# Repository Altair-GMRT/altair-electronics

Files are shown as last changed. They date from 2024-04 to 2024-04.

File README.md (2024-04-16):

# **altair-electronics**

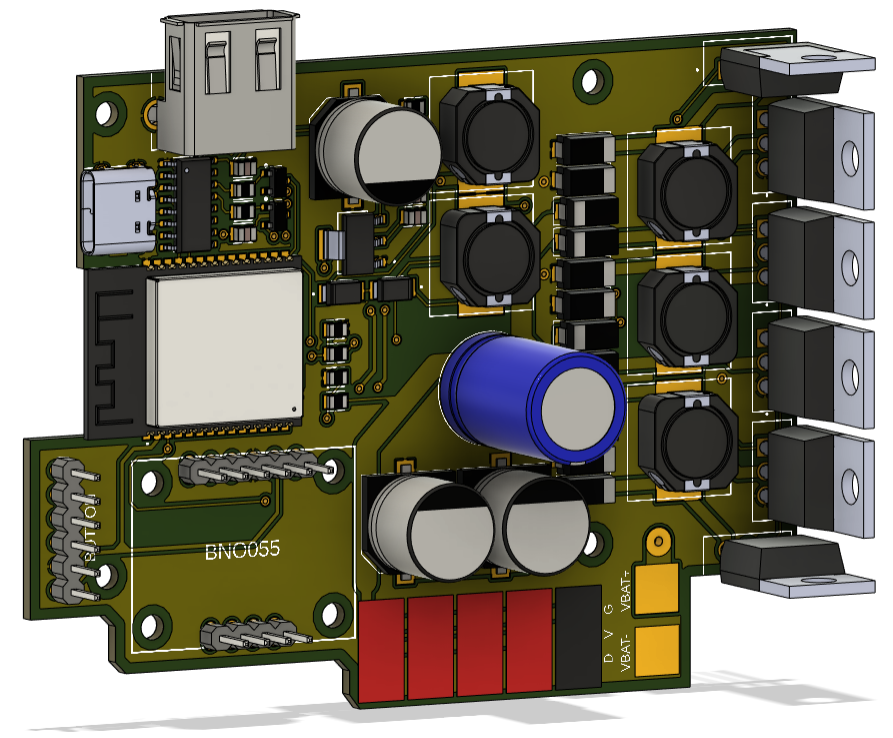
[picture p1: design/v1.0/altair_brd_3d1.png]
Board View 1

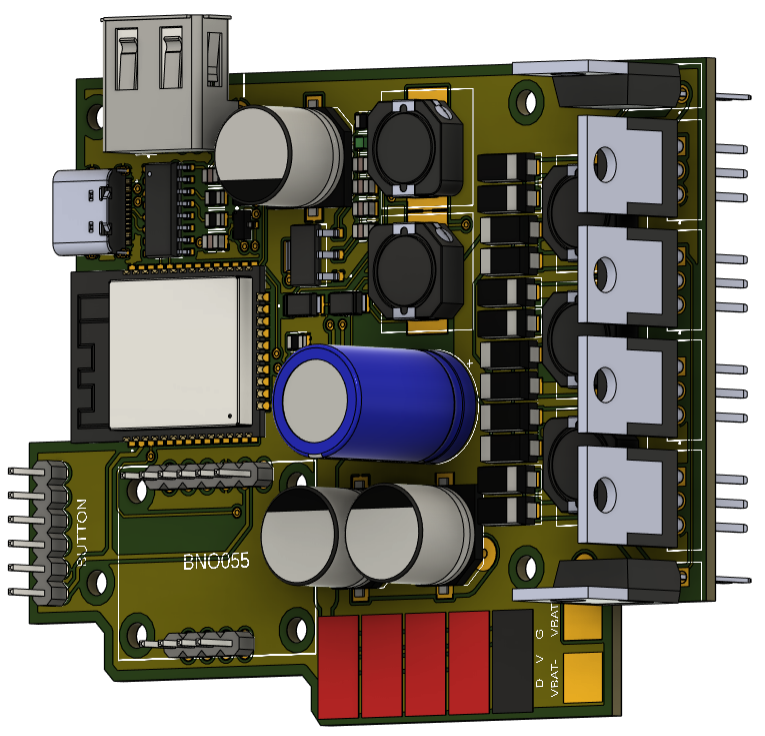
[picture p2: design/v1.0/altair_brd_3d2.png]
Board View 2

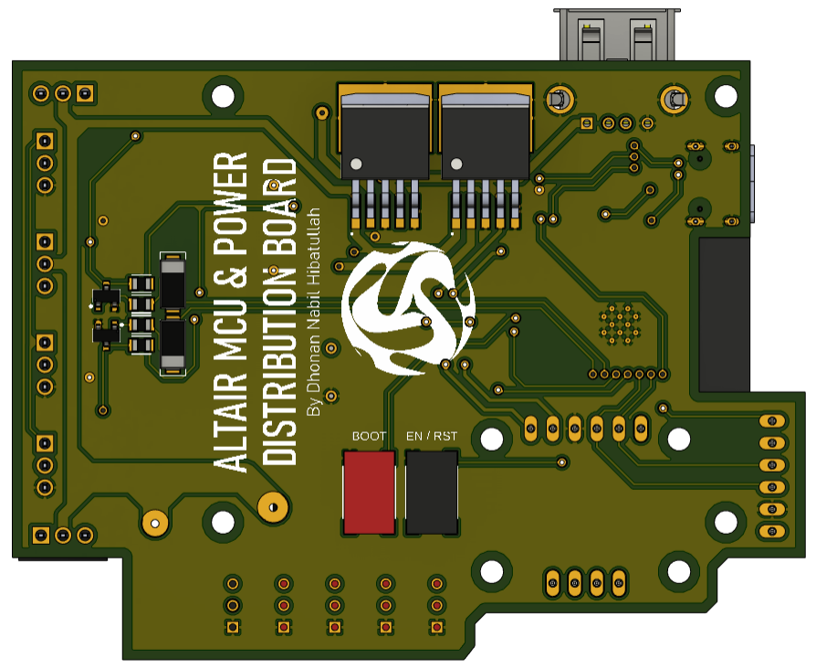
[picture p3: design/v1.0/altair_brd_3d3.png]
Board View 3


## **1. Contents**

- **altair-mcu/**

    This folder contains the Arduino IDE source code for the Altair MCU's firmware. Make sure the following libraries have been installed on your IDE before compiling:

    1. [**Adafruit GFX**](https://github.com/adafruit/Adafruit-GFX-Library)
    2. [**Adafruit SSD1306**](https://github.com/adafruit/Adafruit_SSD1306)
    3. [**Adafruit Sensor**](https://github.com/adafruit/Adafruit_Sensor)
    4. [**Adafruit BNO055**](https://github.com/adafruit/Adafruit_BNO055)

- **design/**

    This folder contains the Eagle/Fusion schematics and board designs, including the libraries used.

## **2. Electronics Design**
The robot will be powered by 4s 35c 5200mAh Li-Po battery. Hence, the battery voltage will be in the range of 12.8V - 16.8V with a maximum discharge of 182A. The Raspberry Pi 5 needs 5V 5A power supply, and 20 Dynamixel MXs need 14V 2A per servo. We will convert the battery voltage to supply those two with a 5V regulator and a Buck-Boost Converter, respectively. Read more about the design at ```design/simulations```.

### **2.1 Buck-Boost Converter**
The buck and the boost in the Buck-Boost Converter will be used interchangeably. The equation describing the behaviour of the buck is:

$$V_{out} = DV_{in}$$

$$I_{ripple} = V_{out}\left(\frac{1}{R} \pm \frac{1 - D}{2L}T \right)$$

$$V_{ripple} \propto \frac{(1-D)V_{out}T^2}{8LC}$$

and for the boost:

$$V_{out} = \frac{1}{1 - D}V_{in}$$

$$I_{ripple} = V_{in}\left(\frac{1}{R(1-D)^2} \pm \frac{1}{2L}DT\right)$$

$$V_{ripple} \propto \frac{DTV_{out}}{RC}$$

Consider the following table: 

|No.|Parameter|Value|
|:---:|:---:|:---:|
|1|$D_{buck}$|$[0.83, 1]$|
|2|$D_{boost}$|$[0, 0.086]$|
|3|$V_{in}$|$[12.8, 16.8]\text{V}$|
|4|$V_{out}$|$14\text{V}$|
|5|$I_{max}$|$30\text{A}$|
|6|$T_S$|$12.5\mu\text{s}$|
|7|$f_S$|$80\text{kHz}$|
|8|$R$|$V_{out}/I_{max} = 0.5\Omega$|

We obtain the optimal (smallest possible, yet acceptable performance) value of $L = 330\mu\text{H}$ and $C = 4.7\text{mF}$ in 3 parallels.

### **2.2 Components**
The following table shows the entire components required for assembling a complete circuit.

| No. | Component Name | Qty. | Datasheets |
| :---: | :--- | :---: | :---: |
| 1 | **ESP32-WROOM-32D** | | |
| 2 | **BNO055** 9-Axis IMU | | |
| 3 | **SSD1306** OLED Display | | |
| 4 | **LM2596S-5.0** 5V 3A Regulator | | |
| 5 | **1N5824** Schottky Diode | | |
| 6 | **CDRH127R** Power Inductor | | |
| 7 | **IRF9540** P-Channel Power MOSFET | | |
| 8 | **S9013** NPN Transistor | | |
| 9 | **SR5100 & 1N58219** Schottky Diode | | |
| 10 | **MOLEX 22-03-5035** Dynamixel Connector | | |
| 11 | **USB Female Type-C** | | |
| 12 | **USB Female Type-A** | | |
| 13 | **SMD Button** | | |

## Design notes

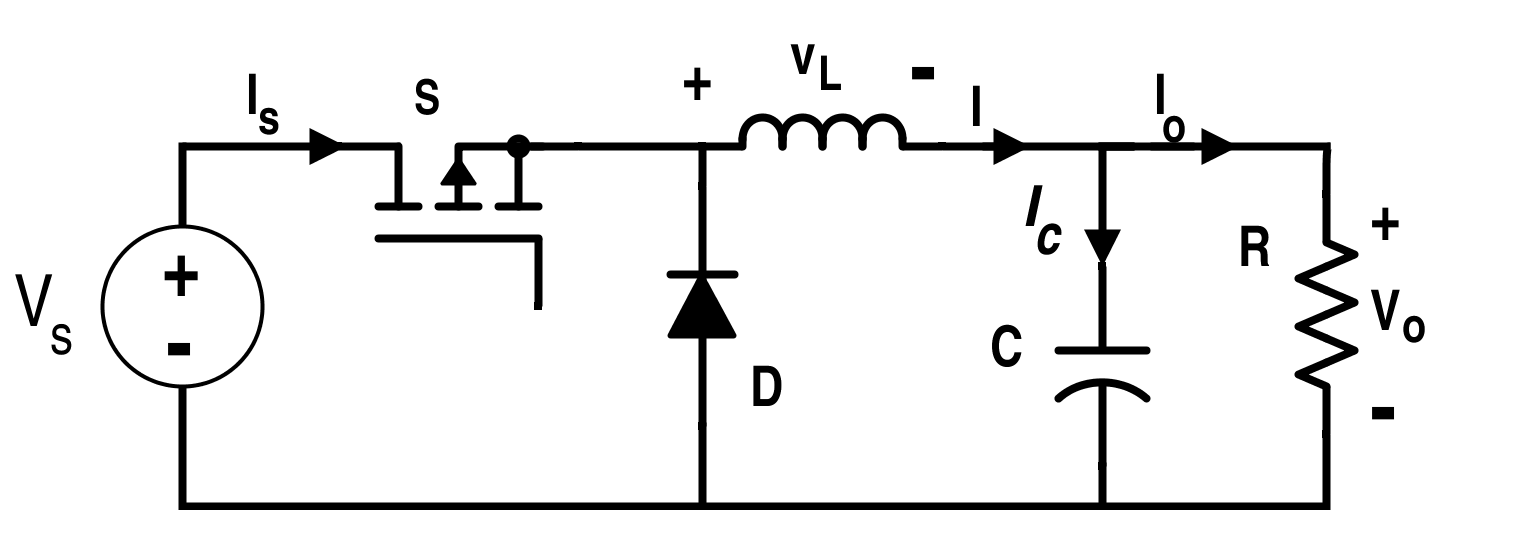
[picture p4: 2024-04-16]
design/simulations/assets/buck_converter.jpg

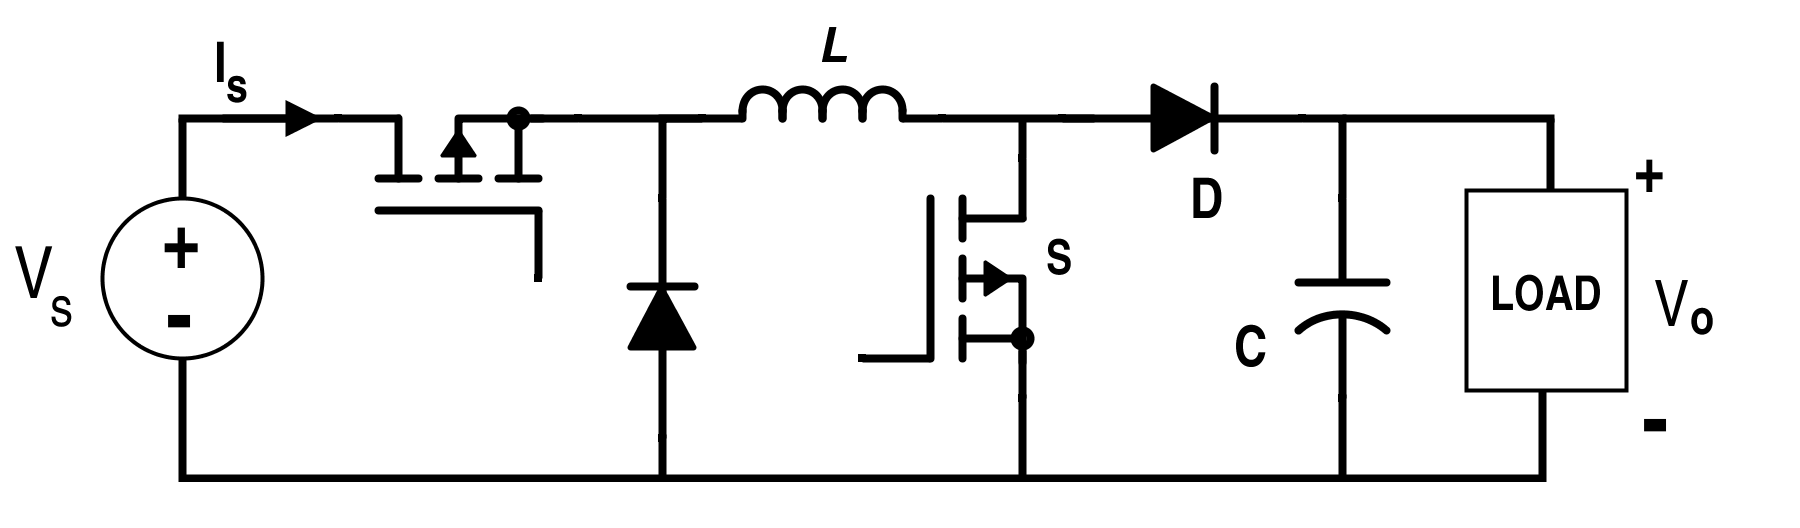
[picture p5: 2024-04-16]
design/simulations/assets/buck_boost_converter.jpg

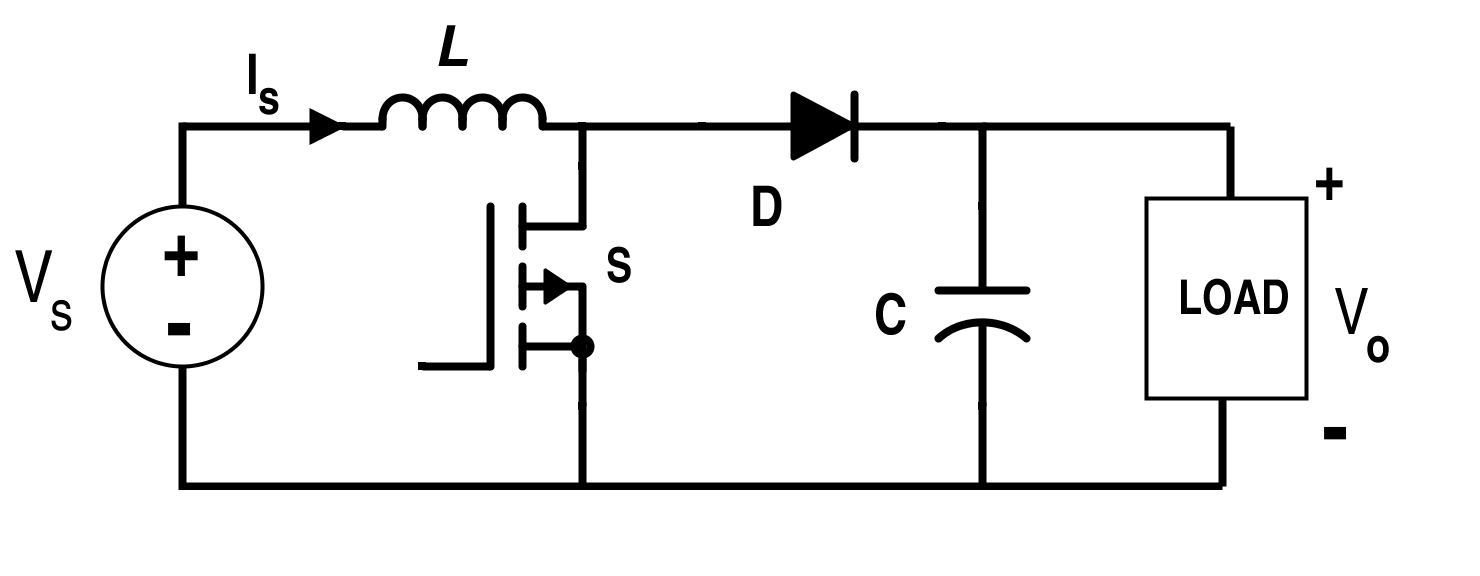
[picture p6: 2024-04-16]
design/simulations/assets/boost_converter.jpg

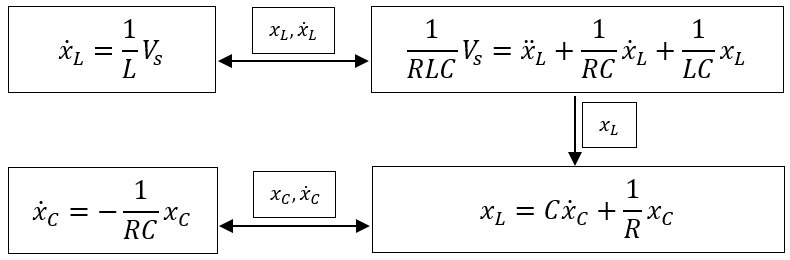
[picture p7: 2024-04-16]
design/simulations/assets/boost_sim_diagram.png

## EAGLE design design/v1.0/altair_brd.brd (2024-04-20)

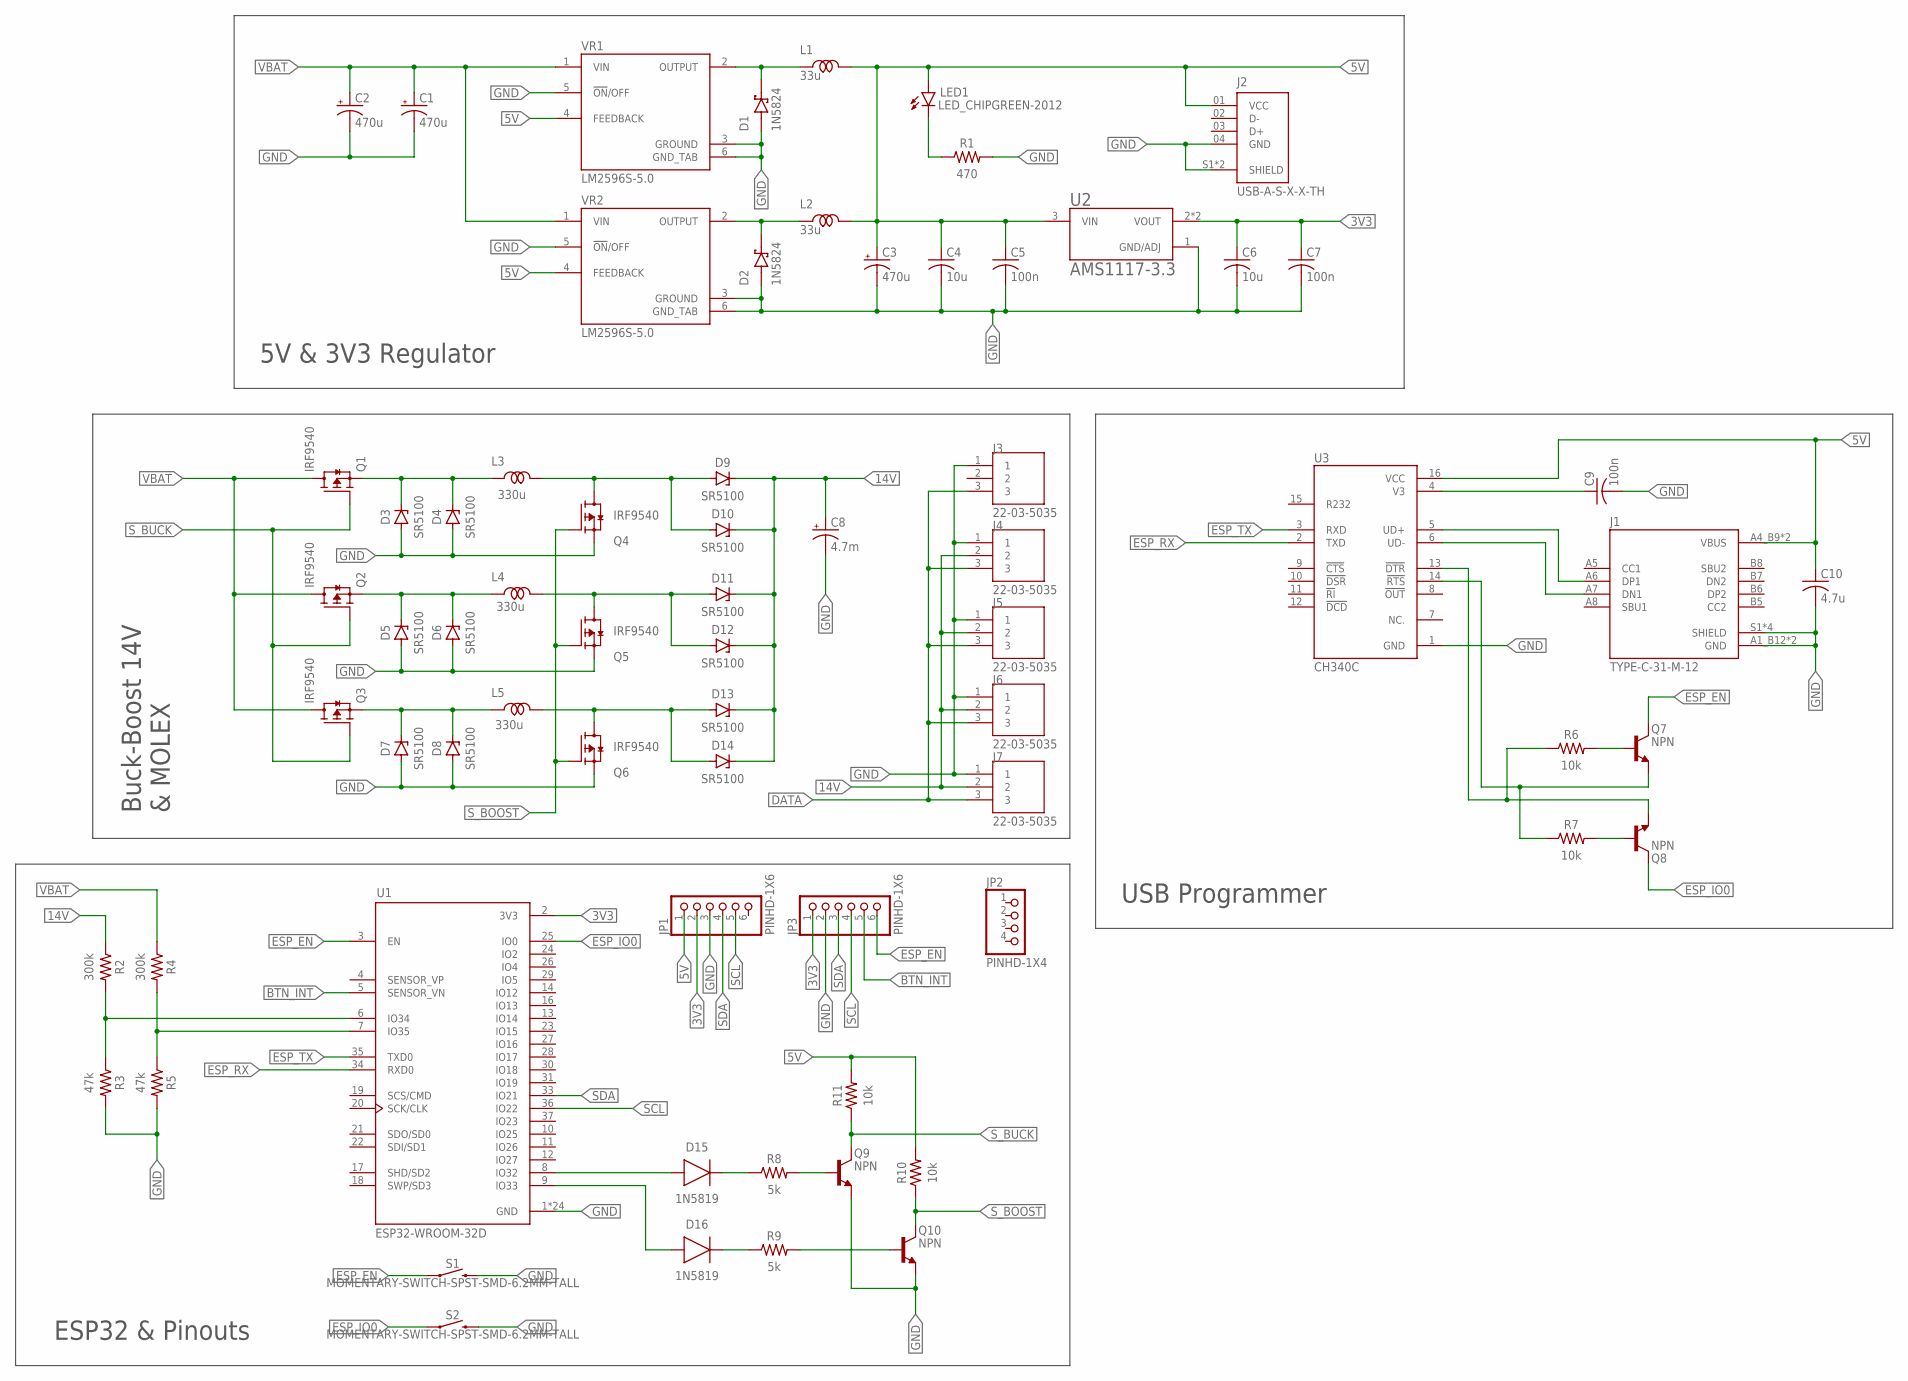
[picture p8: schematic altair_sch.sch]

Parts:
C1, C2, C3: 470u; CAPAE1030X1050N
C4, C6: 10u; CAPC2012X110
C5, C7, C9: 100n; CAPC2012X110
C8: 4.7m; CAPPRD550W60D1200H2000B
C10: 4.7u; CAPC2012X110
D1, D2: 1N5824; SODFL4725X110N
D3, D4, D5, D6, D7, D8, D9, D10, D11, D12, D13, D14: SR5100; DIOM5226X290N
D15, D16: 1N5819; DIOM5226X290N
J1: TYPE-C-31-M-12; HRO_TYPE-C-31-M-12
J2: USB-A-S-X-X-TH; SAMTEC_USB-A-S-X-X-TH
J3, J4, J5, J6, J7: 22-03-5035; MOLEX_22-03-5035
JP1, JP3: PINHD-1X6; 1X06
JP2: PINHD-1X4; 1X04
L1, L2: 33u; CDRH127R
L3, L4, L5: 330u; CDRH127R
LED1: LED_CHIPGREEN-2012; LEDC2012X110N_G
Q1, Q2, Q3, Q4, Q5, Q6: IRF9540; TO254P1052X465X1989-3
Q7, Q8, Q9, Q10: NPN; SOT95P237X112-3N
R1: 470; RESC2012X65
R2, R4: 300k; RESC2012X65
R3, R5: 47k; RESC2012X65
R6, R7, R10, R11: 10k; RESC2012X65
R8, R9: 5k; RESC2012X65
S1, S2: MOMENTARY-SWITCH-SPST-SMD-6.2MM-TALL; TACTILE_SWITCH_SMD_6.2MM_TALL
U1: ESP32-WROOM-32D; MODULE_ESP32-WROOM-32D
U2: AMS1117-3.3; SOT229P700X180-4N
U3: CH340C; SOIC127P600X180-16N
VR1, VR2: LM2596S-5.0; TO170P1524X483-6N

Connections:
3V3: C6.1, C7.1, JP1.2, JP3.1, U1.2 (3V3), U2.2 (VOUT), U2.4 (VOUT)
5V: C3.1 (+), C4.1, C5.1, C10.1, J1.A4_B9 (VBUS), J1.B4_A9 (VBUS), J2.01 (VCC), JP1.1, L1.P$2, L2.P$2, LED1.2 (A), R10.2, R11.2, U2.3 (VIN), U3.16 (VCC), VR1.4 (FEEDBACK), VR2.4 (FEEDBACK)
14V: C8.1 (+), D9.1 (C), D10.1 (C), D11.1 (C), D12.1 (C), D13.1 (C), D14.1 (C), J4.2, J5.2, J6.2, J7.2, R2.1
BTN_INT: JP3.5, U1.5 (SENSOR_VN)
DATA: J3.3, J4.3, J5.3, J6.3, J7.3
ESP_EN: JP3.6, Q7.3 (C), S1.A2 (1), U1.3 (EN)
ESP_IO0: Q8.3 (C), S2.A2 (1), U1.25 (IO0)
ESP_RX: U1.34 (RXD0), U3.2 (TXD)
ESP_TX: U1.35 (TXD0), U3.3 (RXD)
GND: C1.2 (-), C2.2 (-), C3.2 (-), C4.2, C5.2, C6.2, C7.2, C8.2 (-), C9.2, C10.2, D1.A, D2.A, D3.2 (A), D4.2 (A), D5.2 (A), D6.2 (A), D7.2 (A), D8.2 (A), J1.A1_B12 (GND), J1.B1_A12 (GND), J1.S1 (SHIELD), J1.S2 (SHIELD), J1.S3 (SHIELD), J1.S4 (SHIELD), J2.04 (GND), J2.S1 (SHIELD), J2.S2 (SHIELD), J3.1, J4.1, J5.1, J6.1, J7.1, JP1.3, JP3.2, Q4.3 (S), Q5.3 (S), Q6.3 (S), Q9.2 (E), Q10.2 (E), R1.2, R3.2, R5.2, S1.B2 (2), S2.B2 (2), U1.1 (GND), U1.15 (GND), U1.38 (GND), U1.39_1 (GND), U1.39_2 (GND), U1.39_3 (GND), U1.39_4 (GND), U1.39_5 (GND), U1.39_6 (GND), U1.39_7 (GND), U1.39_8 (GND), U1.39_9 (GND), U1.39_10 (GND), U1.39_11 (GND), U1.39_12 (GND), U1.39_13 (GND), U1.39_14 (GND), U1.39_15 (GND), U1.39_16 (GND), U1.39_17 (GND), U1.39_18 (GND), U1.39_19 (GND), U1.39_20 (GND), U1.39_21 (GND), U2.1 (GND/ADJ), U3.1 (GND), VR1.3 (GROUND), VR1.5 (!ON!/OFF), VR1.6 (GND_TAB), VR2.3 (GROUND), VR2.5 (!ON!/OFF), VR2.6 (GND_TAB)
unnamed: D1.C (K), L1.P$1, VR1.2 (OUTPUT)
unnamed: LED1.1 (C), R1.1
unnamed: D3.1 (C), D4.1 (C), L3.P$1, Q1.3 (S)
unnamed: D2.C (K), L2.P$1, VR2.2 (OUTPUT)
unnamed: D5.1 (C), D6.1 (C), L4.P$1, Q2.3 (S)
unnamed: D7.1 (C), D8.1 (C), L5.P$1, Q3.3 (S)
unnamed: D9.2 (A), D10.2 (A), L3.P$2, Q4.2 (D)
unnamed: D11.2 (A), D12.2 (A), L4.P$2, Q5.2 (D)
unnamed: D13.2 (A), D14.2 (A), L5.P$2, Q6.2 (D)
unnamed: R4.2, R5.1, U1.7 (IO35)
unnamed: R2.2, R3.1, U1.6 (IO34)
unnamed: C9.1, U3.4 (V3)
unnamed: J1.A6 (DP1), U3.5 (UD+)
unnamed: J1.A7 (DN1), U3.6 (UD-)
unnamed: Q7.2 (E), R7.1, U3.14 (!RTS)
unnamed: Q8.2 (E), R6.1, U3.13 (!DTR)
unnamed: Q7.1 (B), R6.2
unnamed: Q8.1 (B), R7.2
unnamed: D15.2 (A), U1.8 (IO32)
unnamed: D15.1 (C), R8.1
unnamed: D16.2 (A), U1.9 (IO33)
unnamed: D16.1 (C), R9.1
unnamed: Q10.1 (B), R9.2
unnamed: Q9.1 (B), R8.2
SCL: JP1.5, JP3.4, U1.36 (IO22)
SDA: JP1.4, JP3.3, U1.33 (IO21)
S_BOOST: Q4.1 (G), Q5.1 (G), Q6.1 (G), Q10.3 (C), R10.1
S_BUCK: Q1.1 (G), Q2.1 (G), Q3.1 (G), Q9.3 (C), R11.1
VBAT: C1.1 (+), C2.1 (+), Q1.2 (D), Q2.2 (D), Q3.2 (D), R4.1, VR1.1 (VIN), VR2.1 (VIN)

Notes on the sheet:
5V & 3V3 Regulator
Buck-Boost 14V & MOLEX
USB Programmer
ESP32 & Pinouts

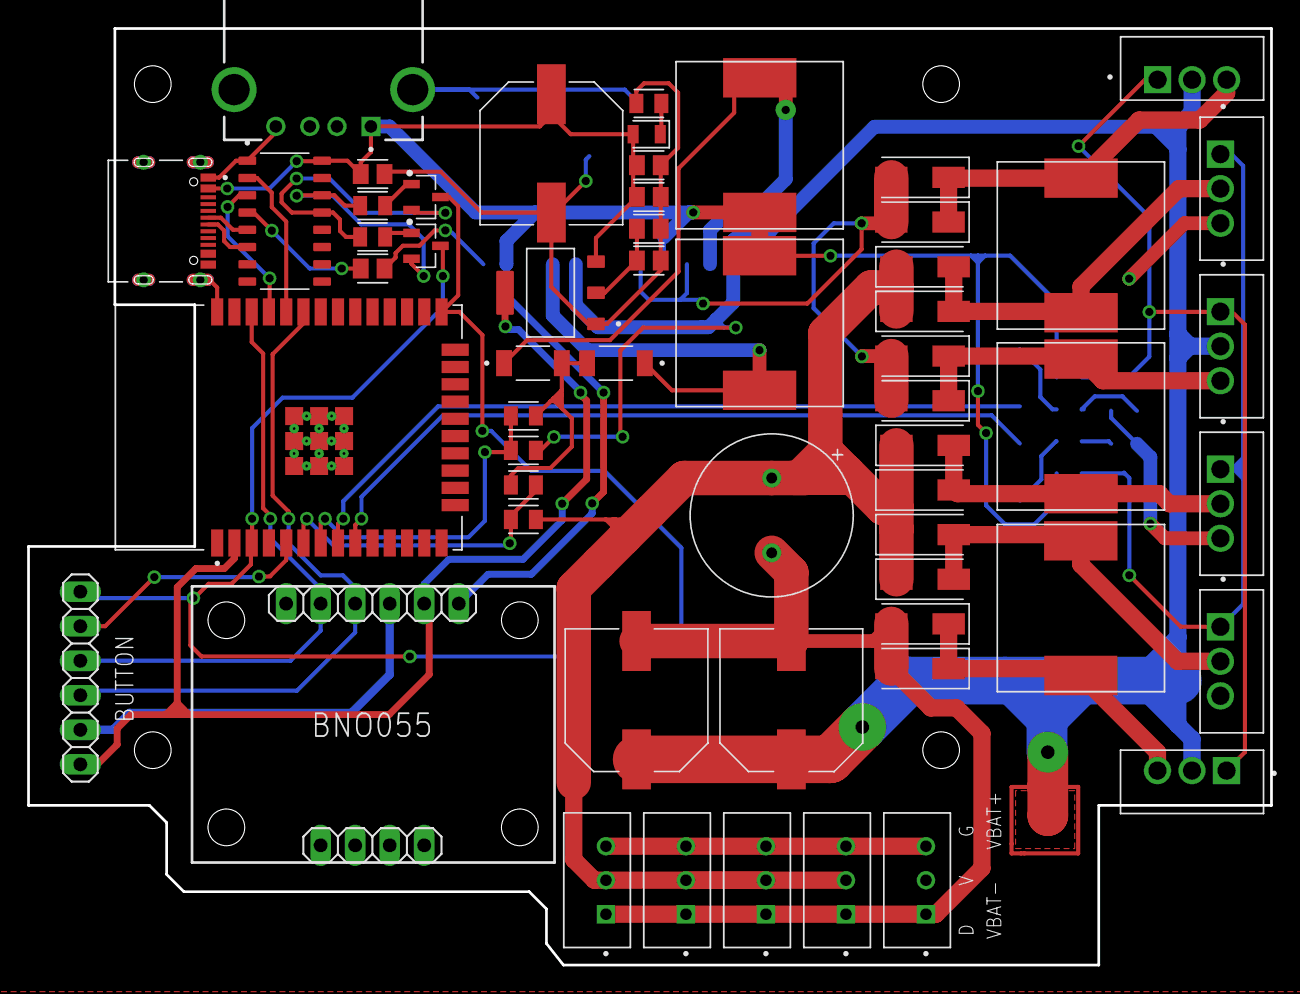
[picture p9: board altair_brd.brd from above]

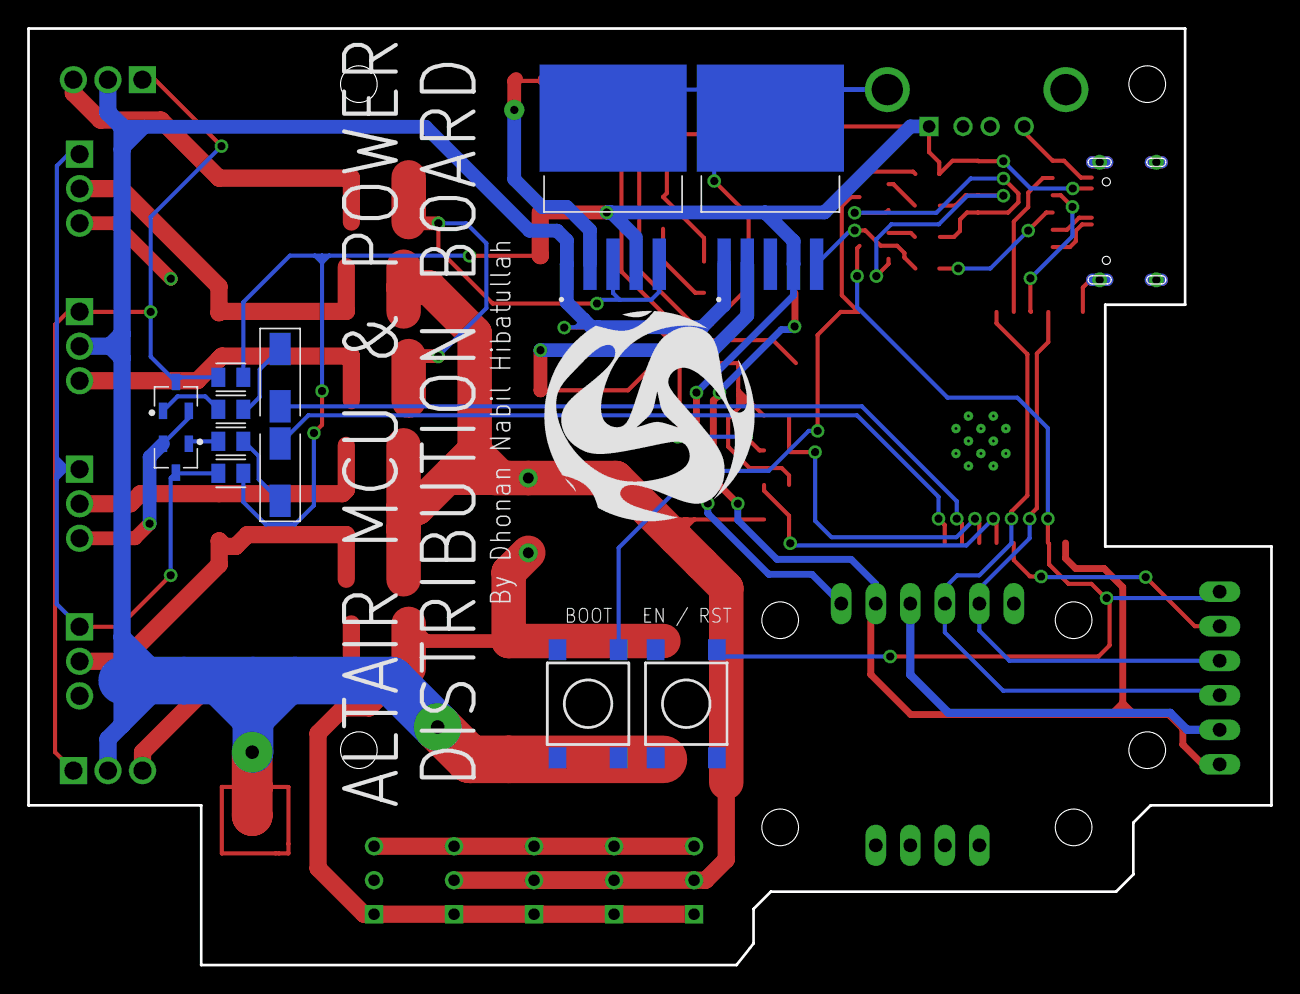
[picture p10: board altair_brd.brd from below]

Board: 2 copper layers, 91.4 x 68.9 mm, 70 parts (12 on the bottom side), 39 nets.

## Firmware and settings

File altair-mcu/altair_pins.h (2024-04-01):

#ifndef __ALTAIR_PINS_H__
#define __ALTAIR_PINS_H__

// Button's multiplexer pins
#define ALTAIR_MUX_IN_PIN 0
#define ALTAIR_MUX_S0_PIN 0
#define ALTAIR_MUX_S1_PIN 0
#define ALTAIR_MUX_S2_PIN 0
#define ALTAIR_BUZZER_PIN 0

#endif

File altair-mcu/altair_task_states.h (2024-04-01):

#ifndef __ALTAIR_TASK_STATES_H__
#define __ALTAIR_TASK_STATES_H__



#define ALTAIR_DISPLAY_TASK_STATE_IDLE              0
#define ALTAIR_DISPLAY_TASK_STATE_SPLASH_SCREEN     1
#define ALTAIR_DISPLAY_TASK_STATE_IMU_CALIB         2
#define ALTAIR_DISPLAY_TASK_STATE_IMU_CALIB_FOUND   3
#define ALTAIR_DISPLAY_TASK_STATE_IMU_CALIB_SUCCESS 4
#define ALTAIR_DISPLAY_TASK_STATE_MAIN_MENU         5

#define ALTAIR_DISPLAY_TASK_REQ_NONE                0
#define ALTAIR_DISPLAY_TASK_REQ_IMU_CALIB           1
#define ALTAIR_DISPLAY_TASK_REQ_IMU_CALIB_FOUND     2
#define ALTAIR_DISPLAY_TASK_REQ_IMU_CALIB_SUCCESS   3
#define ALTAIR_DISPLAY_TASK_REQ_CURSOR_INC          4
#define ALTAIR_DISPLAY_TASK_REQ_CURSOR_DEC          5
#define ALTAIR_DISPLAY_TASK_REQ_ENTER               6
#define ALTAIR_DISPLAY_TASK_REQ_BACK                7



#define ALTAIR_BUTTON_TASK_STATE_IDLE     0
#define ALTAIR_BUTTON_TASK_STATE_DEACTIVE 1
#define ALTAIR_BUTTON_TASK_STATE_ACTIVE   2

#define ALTAIR_BUTTON_TASK_REQ_NONE       0
#define ALTAIR_BUTTON_TASK_REQ_ACTIVATE   1
#define ALTAIR_BUTTON_TASK_REQ_DEACTIVATE 2



#define ALTAIR_IMU_TASK_STATE_IDLE        0
#define ALTAIR_IMU_TASK_STATE_INIT_CALIB  1
#define ALTAIR_IMU_TASK_STATE_LIGHT_CALIB 2
#define ALTAIR_IMU_TASK_STATE_READ        3

#define ALTAIR_IMU_TASK_REQ_NONE          0
#define ALTAIR_IMU_TASK_REQ_CHECK_CALIB   1
#define ALTAIR_IMU_TASK_REQ_READ          2

#endif

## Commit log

2024-04-01 Feat: ESP32 lbr and STEP added
2024-04-16 First version added
    [altair_brd.brd, altair_sch.sch]
2024-04-19 File type changed (9.x compatible)
    [altair_sch.sch]
2024-04-20 Version fixed
    [altair_brd.brd]
2024-04-20 Button interrupt added
    [altair_brd.brd, altair_sch.sch]

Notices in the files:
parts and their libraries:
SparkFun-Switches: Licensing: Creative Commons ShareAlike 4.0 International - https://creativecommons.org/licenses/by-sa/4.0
